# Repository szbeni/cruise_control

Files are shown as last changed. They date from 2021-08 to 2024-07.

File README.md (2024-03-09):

# cruise_control
STM32F401 black pill based cruise control
* STM32F401CC balck pill
* 2x MCP4725 DAC converter
* LM358 opamp to scale down analog 5v to 3.3V 
* 2x push buttons
* 1x SSD1306 OLED screen
* 1x Universal Car Steering Wheel Remote Control Wireless Dvd Navigation (with analog outputs)
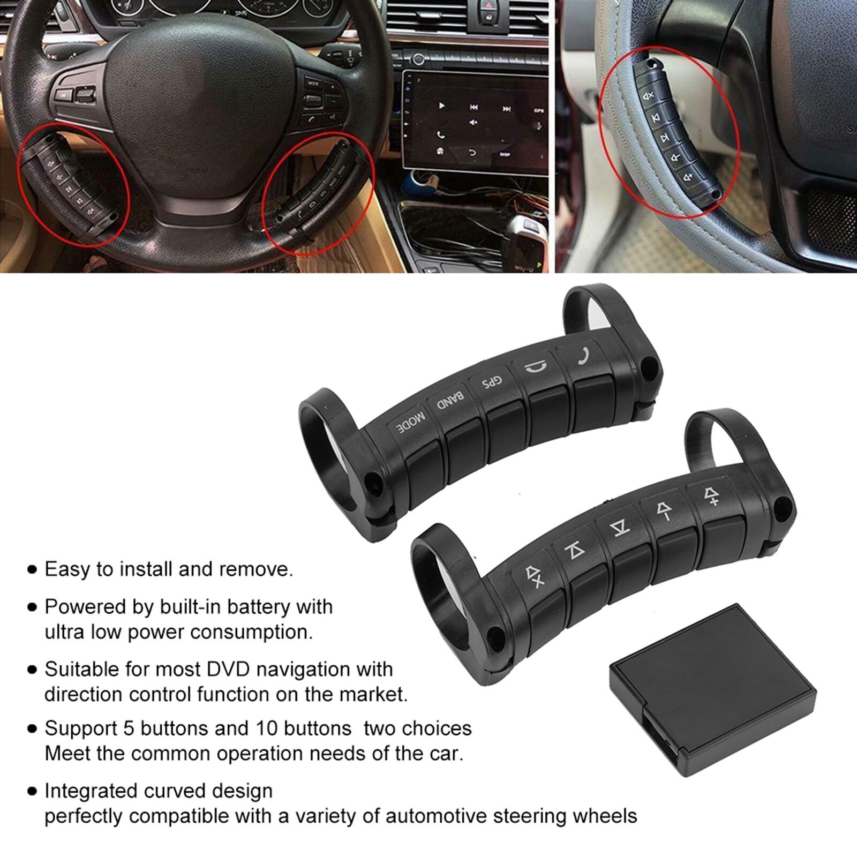
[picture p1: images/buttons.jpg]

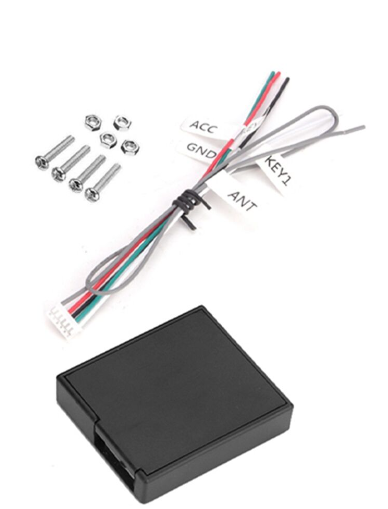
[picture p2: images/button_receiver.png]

* 1x ELM327 Bluetooth OBD2 adapeter (Bluetooth module removed, connected directly to pic18f25k80 from blackpill)
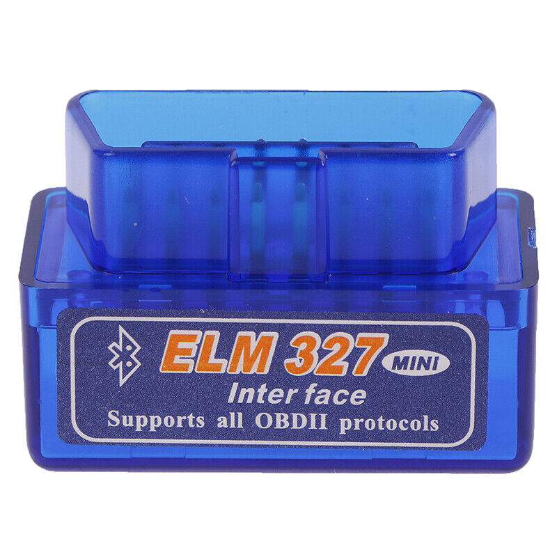
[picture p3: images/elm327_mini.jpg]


Only do this at your on RISK!
The throttle pedal cable needs to be cut and the module needs to be connected inline.
The brake pedal switch needs to be tapped into, to detect pressing of the brake.

The module sits inline of the throttle pedal cables. In a Peugeot Boxer 2013 a throttle pedal signal is basically 2 potentiometers (channel A and B).
In normal mode the module reads this 2 analog values and outputs them via the DAC.
In cruise control mode the module is controlling the speed by changing the throttle.
The actual speed is read from the ODB2 diagnostic bus. As soon as the user steps on the acceleration pedal or the brake pedal the unit switches back to Normal mode.

Schematic: <a href="https://raw.githubusercontent.com/szbeni/cruise_control/main/hw/cruise_control/cruise_control.pdf">cruise_control.pdf</a>

Photos of prototype:
<br>
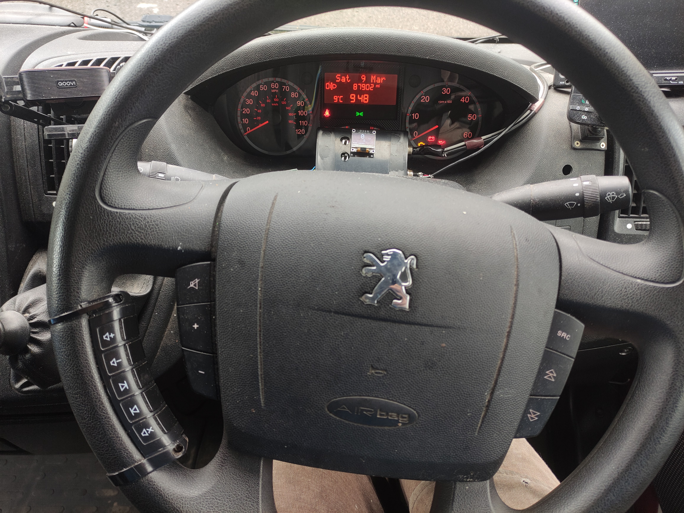
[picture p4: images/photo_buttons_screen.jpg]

<br>
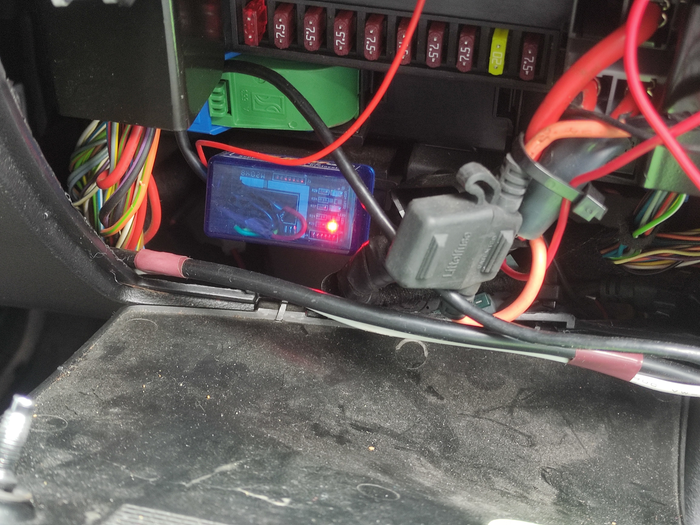
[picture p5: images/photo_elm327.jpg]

<br>
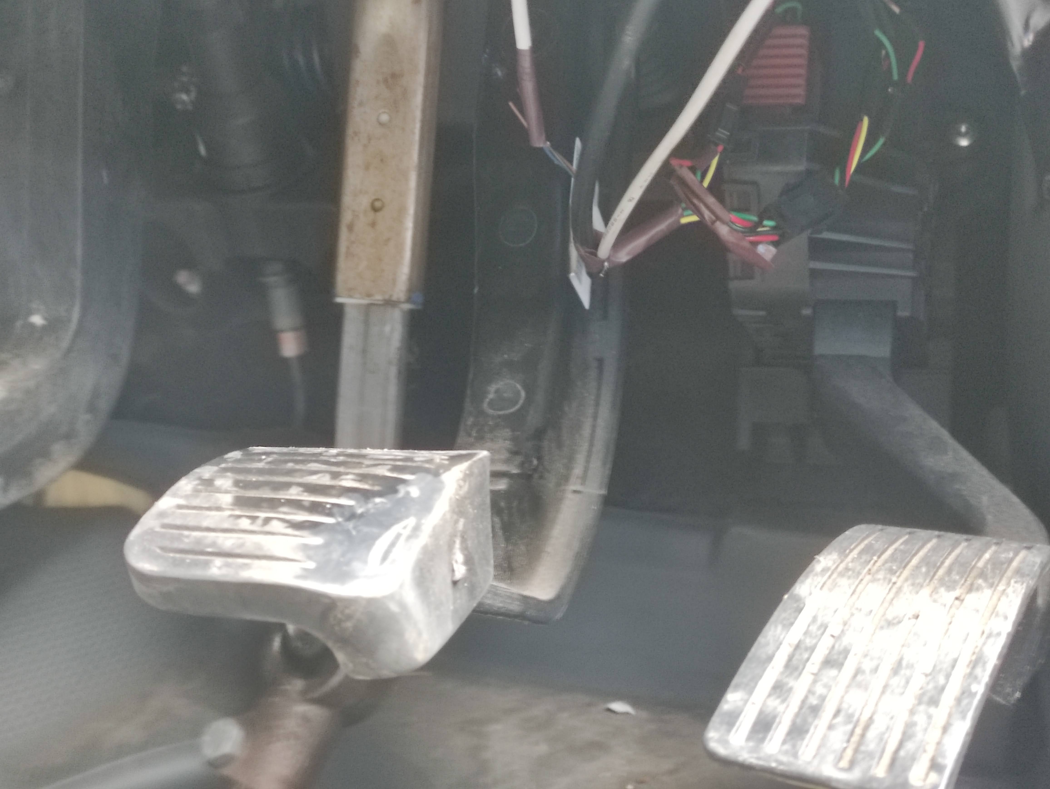
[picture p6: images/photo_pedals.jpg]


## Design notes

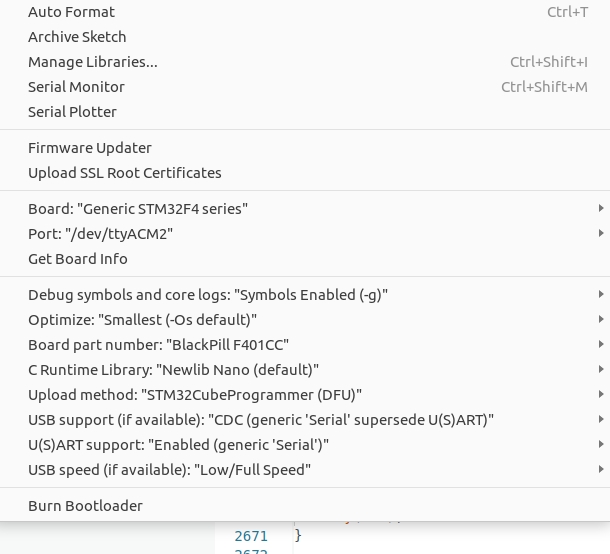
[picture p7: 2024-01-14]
fw/settings.jpg

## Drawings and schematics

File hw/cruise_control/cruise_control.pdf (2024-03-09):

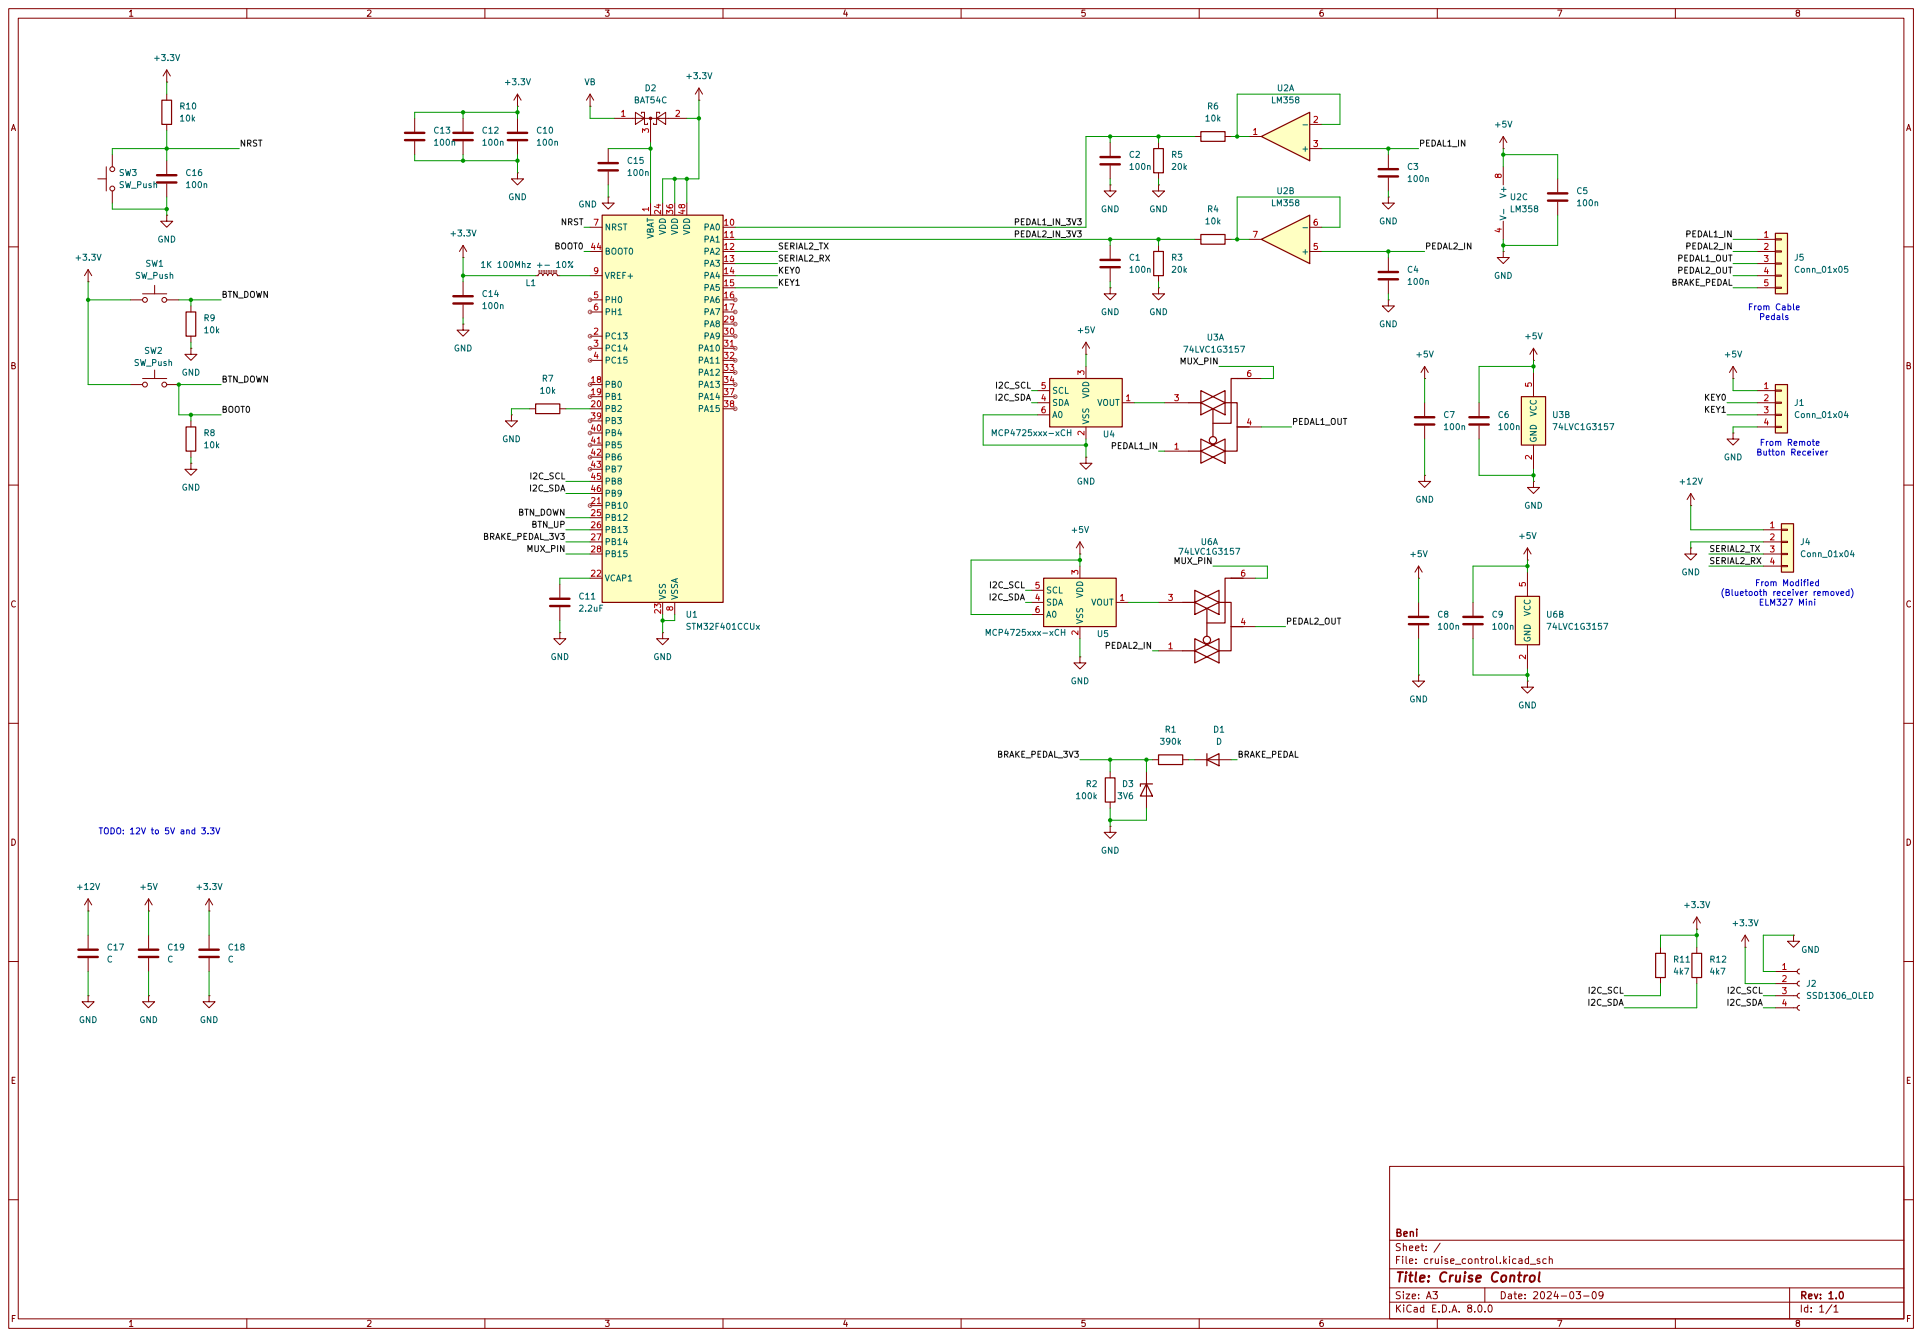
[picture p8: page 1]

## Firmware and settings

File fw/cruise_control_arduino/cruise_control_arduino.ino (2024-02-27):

#include <Wire.h>
#include <Adafruit_GFX.h>
#include <Adafruit_SSD1306.h>
#include <STM32TimerInterrupt.h>
#include <STM32_ISR_Timer.h>
#include "ELMduino.h"
#include "throttle_pedal.h"
#include "config.h"

typedef struct {
  uint8_t mode; 
  float manualThrottle;
  float throttleInPrev;
  float throttleIn;
  float throttleOut;

  //Speed control
  float currentSpeed;
  float targetSpeed;
  float pTerm;
  float iTerm;
  float dTerm;
  float iState;
  float speedOut;
  float dT;
  float error;
  float prevError;
  
  unsigned long lastTick;
  uint8_t unit;
  
  float rpm;
  float rpmPrev;
  uint8_t brakeState;
  bool initialized = false;
  uint8_t screenMode;
  
  bool clearDTCFlag = false;
  bool writePedalToEepromFlag = false;
} CruiseControlStruct;

CruiseControlStruct cc;
TwoWire i2cDev(PB9, PB8);     //SDA  SCL

Adafruit_SSD1306 display(SCREEN_WIDTH, SCREEN_HEIGHT, &i2cDev, OLED_RESET);
ThrottlePedal pedal(DACA_ADDR, DACB_ADDR, AINA_PIN, AINB_PIN, &i2cDev);
ELM327 myELM327;
STM32Timer ITimer(TIM3);

void setup() {
  pinMode(ANALOG_MUX_PIN, OUTPUT);
  digitalWrite(ANALOG_MUX_PIN, LOW);

  Serial.begin(115200);   //USB (PA11/PA12) connected to USB
  pinMode(LED_PIN, OUTPUT);

  pedal.begin();
  pedal.setCalibration(AINA_CALIB, AINB_CALIB); 
  pedal.setMinMax(AINA_MIN, AINA_MAX, AINB_MIN, AINB_MAX);
  pedal.setErrorThresholds(AINA_MAX_ERROR, AINB_MAX_ERROR, DIFFERENCE_MAX_ERROR);
  pedal.setThrottle(0);
  cruiseControlBegin();
  
  delay(200);
  if(!display.begin(SSD1306_SWITCHCAPVCC, SCREEN_ADDRESS)) {
    while(1)
    {
      Serial.println(F("SSD1306 allocation failed"));
      delay(1000);
    } 
  }

  obd2Begin();
  steeringKeysBegin();
  cruiseControlSetMode(MODE_INITIALIZED);
  ITimer.attachInterruptInterval(HW_TIMER_INTERVAL_MS * 1000, TimerHandler);

}


// Timer interrupt loop 20 Hz
static int cntr = 0;
void TimerHandler()
{
  cruiseControlLoop();  
  updateScreen();
  cntr++;
  if(cntr == 20)
  {
    cntr = 0;
    digitalToggle(LED_PIN);
  }
    
}

// Software loop
void loop() {
  obd2Loop();
  float speed = obd2GetSpeed();
  //float speed = 0;
  if(speed != -1)
  {
    cc.currentSpeed = speed;
  }

  float rpm = obd2GetRPM();
  //float rpm = 0;
  if(rpm != -1)
  {
    cc.rpm = rpm;
  }

  if (cc.clearDTCFlag == true)
  {
    cc.clearDTCFlag = false;
    obd2ClearDTC();
  }

  uint8_t screen = cc.screenMode;
  if (cc.mode == MODE_LOCKED)
  {
    screen = SCREEN_MODE_LOCKED;
  }
  screenLoop(screen);
  delay(10);
}

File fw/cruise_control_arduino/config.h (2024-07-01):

#pragma once

#define VERSION 1.41

//LIMITS
#define THROTTLE_MIN 0.0f
#define THROTTLE_MAX 1.0f

#define SPEED_MIN 5.0f
#define SPEED_MAX 120.0f


//MODES

#define CC_DEBUG_ENABLE 0

#define MODE_NOT_INITIALIZED 0
#define MODE_INITIALIZED 1
#define MODE_LOCKED 2
#define MODE_NORMAL 3
#define MODE_THROTTLE 4
#define MODE_RPM 5
#define MODE_SPEED 6
#define MODE_ERROR  7

const String modeName[] = {"Not initialized", "Initialized", "Lock", "Normal", "Throttle", "RPM", "Speed", "Error"};

//Screen modes
#define SCREEN_MODE_DEBUG1   0
#define SCREEN_MODE_DEBUG2   1
#define SCREEN_MODE_SPEED    2
#define SCREEN_MODE_SETTINGS 3
#define SCREEN_LOOP_NUM 4

#define SCREEN_MODE_LOCKED   5


//Unit modes
#define UNIT_MPH  0
#define UNIT_KMPH 1

//Keys
#define SHORT_PRESS       0
#define LONG_PRESS        1
#define HOLD_START        2
#define HOLD_STOP         3




#define KEY_UP 0
#define KEY_DOWN 1
#define KEY_MODE 2
#define KEY_DISPLAY 3
#define KEY_UNIT 4

#define KEY_SPARE1 5
#define KEY_SPARE2 6
#define KEY_SPARE3 7
#define KEY_SPARE4 8
#define KEY_SPARE5 9




//Hardware timer
#define HW_TIMER_INTERVAL_MS 50


//OLED
#define SCREEN_WIDTH 128 // OLED display width, in pixels
#define SCREEN_HEIGHT 64 // OLED display height, in pixels

#define OLED_RESET     -1 // Reset pin # (or -1 if sharing Arduino reset pin)
#define SCREEN_ADDRESS 0x3C ///< See datasheet for Address; 0x3D for 128x64, 0x3C for 128x32


//DAC
#define DACA_ADDR 0x60
#define DACB_ADDR 0x61

//ANALOG INPUTS
#define AINA_PIN A0
#define AINA_CALIB 0.981132075f
#define AINA_MIN   0.97
#define AINA_MAX   3.74
#define AINA_MAX_ERROR 0.2

#define AINB_PIN A1
#define AINB_CALIB 0.977794891f
#define AINB_MIN   0.48
#define AINB_MAX   1.87
#define AINB_MAX_ERROR 0.2

#define DIFFERENCE_MAX_ERROR 0.4

#define KEY0_PIN A4
#define KEY1_PIN A5


//BUTTONS
#define BTN_NUM 2
#define BTN_UP_PIN    PB13
#define BTN_DOWN_PIN  PB12

//BRAKE PEDAL INPUT
#define BRAKE_PEDAL_PIN  PB14
#define ANALOG_MUX_PIN PB15

//LED
#define LED_PIN PC13

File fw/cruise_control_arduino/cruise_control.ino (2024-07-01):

void debugPrint(String str)
{
  #ifdef CC_DEBUG_ENABLE 
    Serial.println(str);
  #endif
}

void cruiseControlBegin()
{
  pinMode(BRAKE_PEDAL_PIN, INPUT);
  cc.screenMode = SCREEN_MODE_SPEED;
  //cc.screenMode = SCREEN_MODE_DEBUG1;

  cc.mode = MODE_NOT_INITIALIZED;
  cc.throttleInPrev = -1;
  cc.manualThrottle = 0;
  cc.currentSpeed = -1;
  cc.targetSpeed = 0;
  cc.throttleOut = 0;  
  cc.unit = UNIT_MPH;
  cc.pTerm = 0.030f;
  cc.iTerm = 0.015f;
  cc.dTerm = 0.001f;
  cc.iState = 0.0f;
  cc.clearDTCFlag = false;
  cc.writePedalToEepromFlag = false;
  
}


String pressTypeStr[4] = {"Short", "Long", "Hold Start", "Hold Stop" };
void steeringKeysCallback(int16_t key, uint8_t pressType)
{
  if(cc.mode == MODE_LOCKED)
  {
    if(key == KEY_UP && pressType == SHORT_PRESS)
    {
      //if (cc.brakeState == HIGH &&  cc.throttleIn > 0.5)
      if (cc.brakeState == HIGH)
      {
        cc.mode = MODE_NORMAL;
      }
    }
  }
  if(key == KEY_DISPLAY && pressType == SHORT_PRESS)
  {
    Serial.println(cc.screenMode);
    cc.screenMode += 1;
    
    if (cc.screenMode >= SCREEN_LOOP_NUM)
    {
      cc.screenMode = 0;
    }
  }
  
  if(key == KEY_DISPLAY && pressType == LONG_PRESS)
  {
    Serial.println("Clear DTC requsted");
    cc.clearDTCFlag = true;
  }


  if(cc.mode == MODE_THROTTLE)
  {
    float change = 0.02f;
    if(pressType == LONG_PRESS) change *= 2.0;
    if (key == KEY_UP) cc.manualThrottle = changeThrottle(cc.manualThrottle, change);
    if(key == KEY_DOWN) cc.manualThrottle = changeThrottle(cc.manualThrottle, -change);
  }

  if(cc.screenMode == SCREEN_MODE_SPEED)
  {
    if(key == KEY_UNIT) cc.unit = !cc.unit;
    if(cc.mode == MODE_SPEED)
    {
      float change = 1.0f;
      if(pressType == LONG_PRESS) change *= 2.0;
      if(key == KEY_UP) cc.targetSpeed = changeTargetSpeed(cc.targetSpeed, change);
      if(key == KEY_DOWN) cc.targetSpeed = changeTargetSpeed(cc.targetSpeed, -change);
      if(key == KEY_MODE) cc.mode = MODE_NORMAL; 
    }
  }

  if(cc.screenMode == SCREEN_MODE_SETTINGS)
  {
    float change = 1.0f;
    if(pressType == LONG_PRESS) change *= 2.0;
    if(key == KEY_UP) cc.pTerm = changeValue(cc.pTerm, 0.001f, 0, 100);
    if(key == KEY_DOWN) cc.pTerm = changeValue(cc.pTerm, -0.001f, 0, 100);
    if(key == KEY_MODE) cc.iTerm = changeValue(cc.iTerm, 0.001f, 0, 100);
    if(key == KEY_UNIT) cc.iTerm = changeValue(cc.iTerm, -0.001f, 0, 100);
    if(key == KEY_SPARE1) cc.dTerm = changeValue(cc.dTerm, 0.001f, 0, 100);
    if(key == KEY_SPARE2) cc.dTerm = changeValue(cc.dTerm, -0.001f, 0, 100);
    


    
  }

  if(cc.screenMode == SCREEN_MODE_DEBUG1)
  {
    if(key == KEY_UP) {
      cc.writePedalToEepromFlag = true;
    }
  }




  if(cc.mode == MODE_NORMAL)
  {
    if(key == KEY_UP)
    {
      if(cc.currentSpeed > SPEED_MIN)
      {
        cc.targetSpeed = cc.currentSpeed;
        cc.mode = MODE_SPEED;  
      }
    }
  }

  
//  Serial.print(pressTypeStr[pressType]);  
//  Serial.print(" pressed: "); 
//  Serial.println(key); 
  
}

void holdKeyCheck()
{
  int16_t key = steeringKeysCheckHold();
  if(cc.mode == MODE_THROTTLE)
  {
    if (key == KEY_UP) cc.manualThrottle = changeThrottle(cc.manualThrottle, 0.01f);
    if(key == KEY_DOWN) cc.manualThrottle = changeThrottle(cc.manualThrottle, -0.01f);
  }

  if(cc.mode == MODE_SPEED)
  {
    if (key == KEY_UP) cc.targetSpeed = changeTargetSpeed(cc.targetSpeed, 0.1f);
    if(key == KEY_DOWN) cc.targetSpeed = changeTargetSpeed(cc.targetSpeed, -0.1f);
  }
  
}




void cruiseControlLoop()
{ 
  unsigned long now = millis();
  cc.dT = 1.0f / (float)(now - cc.lastTick);
  cc.lastTick = now;

  if (cc.mode == MODE_NOT_INITIALIZED)
  {
    pedal.setThrottle(0);
    return;
  }
    
    
  if (cc.mode == MODE_INITIALIZED)
  {
    cc.mode = MODE_LOCKED;
  }

  cc.brakeState = digitalRead(BRAKE_PEDAL_PIN);

  // When brake is pressed to to normal state
  if (cc.brakeState == HIGH)
  {
    if(cc.mode != MODE_ERROR && cc.mode != MODE_LOCKED )
    {
      cc.mode = MODE_NORMAL;  
    }
  }
  
  steeringKeysLoop();
  holdKeyCheck();
  cc.throttleIn = pedal.getThrottle();
  if(cc.throttleIn < 0.0f)
  {
    cc.mode = MODE_ERROR;
    cc.throttleOut = 0;
  }
  else
  {
    //get out of error mode if pedal is detected
//    if (cc.mode == MODE_ERROR)
//    {
//      cc.mode = MODE_NORMAL;
//    }
  }

  if (cc.mode == MODE_LOCKED)
  {
    cc.throttleOut = 0;
  }
  else if (cc.mode == MODE_NORMAL)
  {
    cc.throttleOut = cc.throttleIn;
    //Hold last value
    cc.manualThrottle = cc.throttleIn;
    //Change the speed controller to the current throttle
    cc.iState = cc.throttleIn;
  }
  else if (cc.mode == MODE_THROTTLE)
  {
    cc.throttleOut = cc.manualThrottle;
    if ((cc.throttleIn - 0.05f) > cc.throttleInPrev)
    {
      cc.mode = MODE_NORMAL;
    }

  }
  else if (cc.mode == MODE_SPEED)
  {
    
    cc.throttleOut = speedController(cc.targetSpeed, cc.currentSpeed, cc.dT);
    if ((cc.throttleIn - 0.05f) > cc.throttleInPrev)
    {
      cc.mode = MODE_NORMAL;
    }
    if(cc.rpm > 3300.0)
    {
      cc.mode  = MODE_NORMAL;
    }
    // float rpmDiff = cc.rpm - cc.rpmPrev;
    // if(cc.rpm > 2000 && rpmDiff > 100)
    // {
    //   cc.mode  = MODE_NORMAL;
    // }
  }
  else if (cc.mode == MODE_ERROR)
  {
    cc.throttleOut = 0;
  }


  // Analog MUX, select DAC output when in speed mode, otherwise use pedal from car
  if ((cc.mode == MODE_LOCKED && cc.rpm > 600.0) || (cc.mode == MODE_SPEED))
  {
    digitalWrite(ANALOG_MUX_PIN, HIGH);
  }
  else
  {
    digitalWrite(ANALOG_MUX_PIN, LOW);
  }
  
  
  bool writeEEPROM = false;
  //Do it only once when user requested
  if (cc.writePedalToEepromFlag)
  {
    Serial.println("Write to EEPROM.");
    cc.writePedalToEepromFlag = false;
    writeEEPROM = true;
  }
  pedal.setThrottle(cc.throttleOut, writeEEPROM);
  cc.throttleInPrev = cc.throttleIn;
  cc.rpmPrev = cc.rpm;
}



float speedController(float target, float current, float dT)
{
  float error;
  error = target - current;
  
  if(error > 10.0f) error = 10.0f;
  else if(error < -10.0f) error = -10.0f;
 
  cc.error = error;


  if(error < 0)
  {
    //make integrator term harher when we are speeding
    cc.iState += -error * error * cc.iTerm * dT;
    
  }
  else
  {
    cc.iState += error * cc.iTerm * dT;
  
  }
  
  cc.speedOut = error * cc.pTerm + cc.iState + (cc.error - cc.prevError) * cc.dTerm;
  cc.prevError = error;
  
  //down hill when we suddenly starting to accelerate
  //if (error < -2) cc.iState = 0.0f;
    
  if(cc.iState < THROTTLE_MIN) cc.iState = 0.0f;
  else if(cc.iState > THROTTLE_MAX) cc.iState = 1.0f;

  if(cc.speedOut < THROTTLE_MIN) cc.speedOut = 0.0f;
  else if(cc.speedOut > THROTTLE_MAX) cc.speedOut = 1.0f;
    
  return cc.speedOut;
}
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

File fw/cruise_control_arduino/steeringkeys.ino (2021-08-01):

#include "config.h"

#define LONG_PRESS_TIME 400
#define HOLD_TIME 1500

#define TOLERANCE 90
#define NUM_KEYS 2
int16_t keys[5] = {1960, 480, 890, 680, 1160};

int16_t keyHold[NUM_KEYS] = {-1, -1};
int16_t keyPrev[NUM_KEYS] = {-1, -1};
long keyChangeTime[NUM_KEYS] = {0, 0};
uint8_t keyLongPressSent[NUM_KEYS] = {0, 0};

void steeringKeysBegin()
{
  pinMode(KEY0_PIN, INPUT);
  pinMode(KEY1_PIN, INPUT);
}

int16_t getButton(int16_t raw)
{
  for (int16_t i = 0; i < 5; i++)
  {
    int16_t val = keys[i];
    if (abs(raw - val) < TOLERANCE)
      return i;
  }
  return -1;
}

int16_t steeringKeysCheckHold()
{
  if (keyHold[0] != -1)
    return keyHold[0];
  if (keyHold[1] != -1)
    return keyHold[1] + 5;
  return -1;
}

int16_t steeringKeysCheckPress()
{
  if (keyPrev[0] != -1)
    return keyPrev[0];
  if (keyPrev[1] != -1)
    return keyPrev[1] + 5;
  return -1;
}

void steeringKeysLoop()
{
  uint16_t raw0 = analogRead(KEY0_PIN);
  uint16_t raw1 = analogRead(KEY1_PIN);
  int16_t key[2];
  key[0] = getButton(raw0);
  key[1] = getButton(raw1);

  for (int i = 0; i < NUM_KEYS; i++)
  {
    if (keyPrev[i] != key[i])
    {
      //Serial.print("Change: "); Serial.print(keyPrev[i]); Serial.print("->");Serial.print(key[i]);Serial.println("");
      if (keyHold[i] == -1 && keyPrev[i] != -1 && keyLongPressSent[i] == 0)
      {
        //Serial.print("Short Press: "); Serial.println(keyPrev[i]);
        steeringKeysCallback(keyPrev[i] + i * 5, SHORT_PRESS);
      }
      keyLongPressSent[i] = 0;
      keyChangeTime[i] = millis();
    }

    if (key[i] != -1 && (millis() - keyChangeTime[i]) > LONG_PRESS_TIME)
    {
      if (keyLongPressSent[i] == 0)
      {
        keyLongPressSent[i] = 1;
        //Serial.print("Long Press: "); Serial.println(keyPrev[i]);

        steeringKeysCallback(keyPrev[i] + i * 5, LONG_PRESS);
      }
    }

    if (key[i] != -1 && (millis() - keyChangeTime[i]) > HOLD_TIME)
    {
      if (keyHold[i] != key[i])
      {
        //Serial.print("Hold started: "); Serial.println(key[i]);
        keyHold[i] = key[i];
        
        steeringKeysCallback(keyHold[i] + i * 5, HOLD_START);

        
      }
    }
    else
    {
      if (keyHold[i] != -1)
      {
        //Serial.print("Hold stopped: "); Serial.println(keyHold[i]);
        steeringKeysCallback(keyHold[i] + i * 5, HOLD_START);
        keyHold[i] = -1;
      }
    }
    keyPrev[i] = key[i];
  }
}

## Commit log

2024-01-14 added clear DTC and cleaned up some commit mistakes
    [ELMduino.cpp, ELMduino.h, cruise_control.ino]
2024-01-14 lock screen fix simplified lock
    [config.h, cruise_control.ino, cruise_control_arduino.ino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]
2024-01-21 initialisation fix, added option to write eeprom for DACs
    [cruise_control.ino, cruise_control_arduino.ino, throttle_pedal.cpp]
2024-03-09 added schematic, TODO: vregs
    [cruise_control.kicad_pcb, cruise_control.kicad_sch]
2024-03-09 schematic link
2024-07-01 dont disable speed mode because of noise
    [config.h, cruise_control.ino]
